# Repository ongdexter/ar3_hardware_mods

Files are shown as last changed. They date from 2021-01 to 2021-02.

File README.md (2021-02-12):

# AR3 Hardware Mods
Some modifications that I've made to the AR3 hardware. They are designed to be added on with minimal disassembly.

## Inductive Limit Switches
I repositioned the J5 limit switch to calibrate directly against the J6 bearing cap, which should be more accurate than using the belt carrier. I also took the opportunity to try out an inductive sensor, which I thought would be easier to position for the calibration angle than the mechanical switches. Having inductive limit switches will also help avoid cases of damaged or bent limit switches. It seems to have worked well so I'll eventually redesign and replace the other limit switches as well.

(https://www.youtube.com/watch?v=8Dm-i5OytqE "J5 Inductive Limit Switch")

-----

### J5 Limit Switch
* I use an **NJK-5002C** sensor along with the provided 10x2mm magnet though any other of similar dimensions that runs on 5V should work fine as a drop-in replacement, take note if you're getting an NO or NC one, you will have to make changes in the firmware accordingly
* Magnet mount will be secured to the J6 bearing cap with two M4x10 flathead screw, replacing the existing set screws
* Magnet can be press fit into the magnet mount  
  **NOTE**: be sure to mount it in the orientation with the correct polarity, test with the sensor first
* Sensor mount can be secured to the J6 main bearing arm with two M4x20 flathead screws, replacing the existing ones
* The sensor mount is designed to have just enough tolerance for the sensor to slide up and down with some force applied, this is to allow you to adjust the distance of the sensor from the magnet to calibrate the sensitivity. You'll want to adjust it such that the sensor is triggered only when the magnet is directly above
* The bearing cap is not fixed directly to the J6 housing so you'll have to manually rotate it so that the top and bottom screws are vertically aligned (see the first image below). This may require some trial-and-error - a good way I've found is to calibrate against the limit switch, send J5 to the 0-degree position through software, and then check if the J6 housing is aligned against the J5 cover spacer. After a good alignment is achieved, however, the bearing cap rotates with the J6 housing and can provide an accurate measurement of the rotation

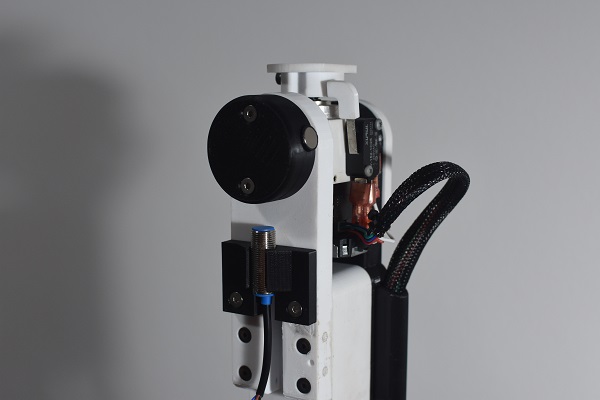
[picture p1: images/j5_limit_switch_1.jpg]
  
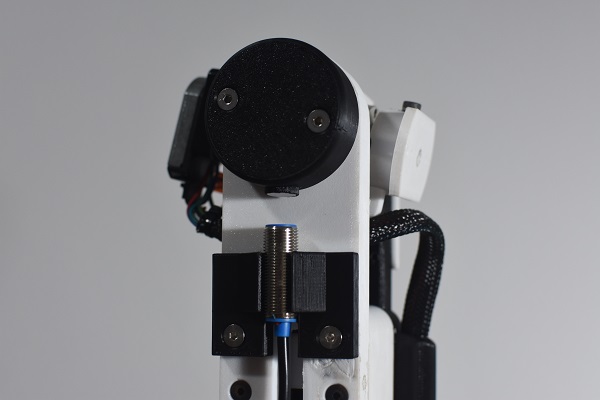
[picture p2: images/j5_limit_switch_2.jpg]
  

-----

## Joint Position Encoders
The original rotor encoder design provides good resolution and, despite backlash and other sources of inaccuracy, works well for applications that only require repeatability. Task positions can be taught and the actual joint positions do not matter too much. However, goals produced by motion planning require accurate correspondence between the actual and intended positions of the arm. At the cost of some resolution, we can achieve much more accurate control of the arm with joint position encoders. With the AMT-102V encoders at the maximum 2048 pulses per revolution, we can get 8192 counts with quadrature decoding, giving us a respectable resolution of 0.05 degrees per encoder count which is acceptable given that there are probably other more significant sources of error.

-----

### J2 Joint Encoder
* The spindle adapter can be screwed over the existing J2 drive spindle, replacing every other screw. You'll need longer M3 flathead screws
* Glue the two parts of the assembly together
* The entire piece will snap on the the J2 turret housing

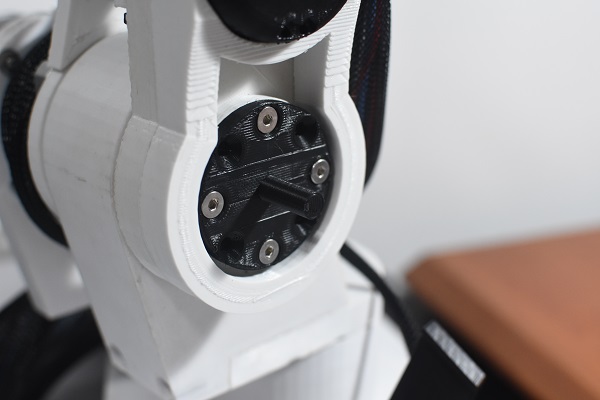
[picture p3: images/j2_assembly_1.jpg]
  
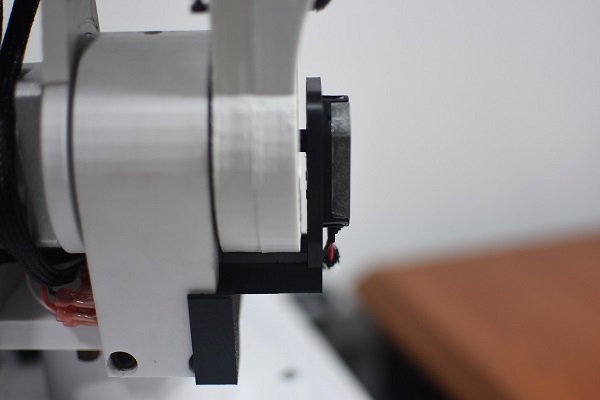
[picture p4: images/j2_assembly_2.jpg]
  
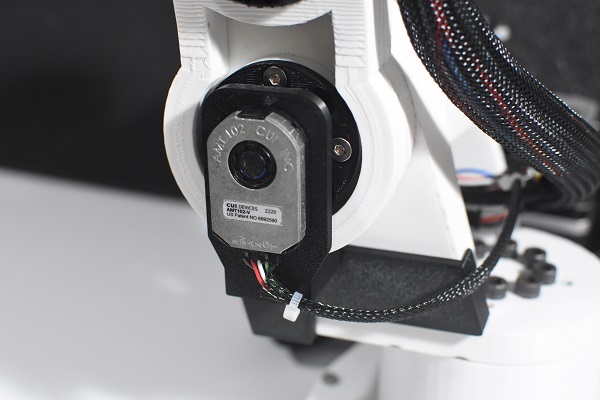
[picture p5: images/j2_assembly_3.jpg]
  

-----

### J5 Joint Encoder
* You can just glue the extension on to the J6 housing
* You'll want to use the longer M3 screws for the covers to secure the adapter
* I chose to leave the wires outside but with a little more effort you could squeeze them into the cover spacer and make everything a little neater

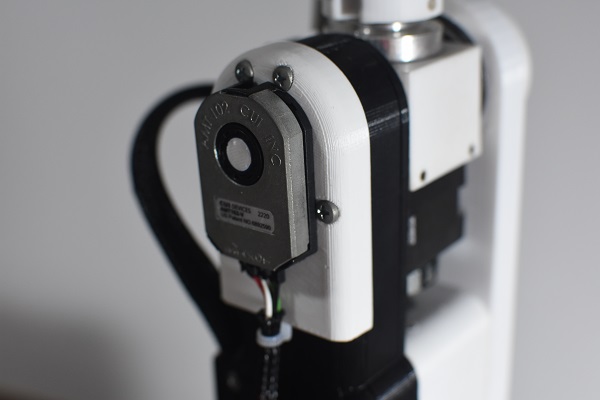
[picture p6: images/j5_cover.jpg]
  

-----

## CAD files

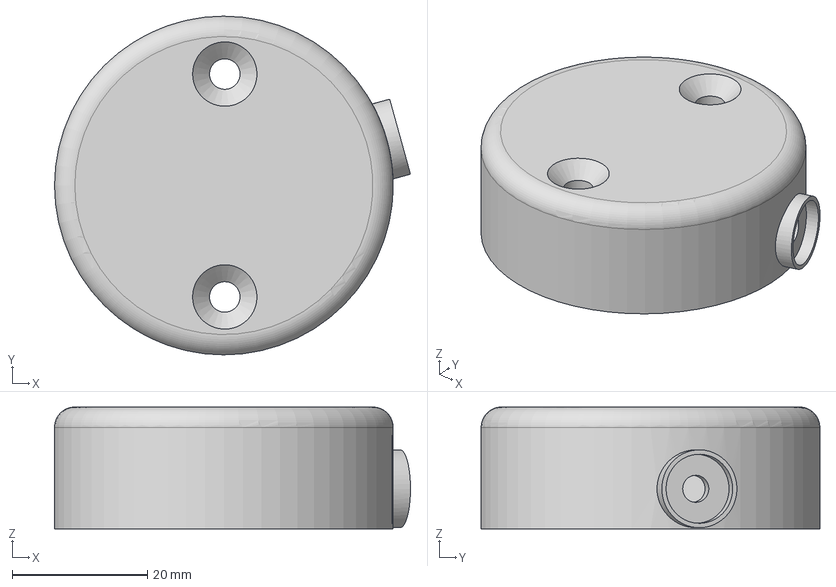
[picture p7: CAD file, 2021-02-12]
joint_limit_switches/J5/J5 limit switch magnet mount.step
52.6 x 50.0 x 18.0 mm

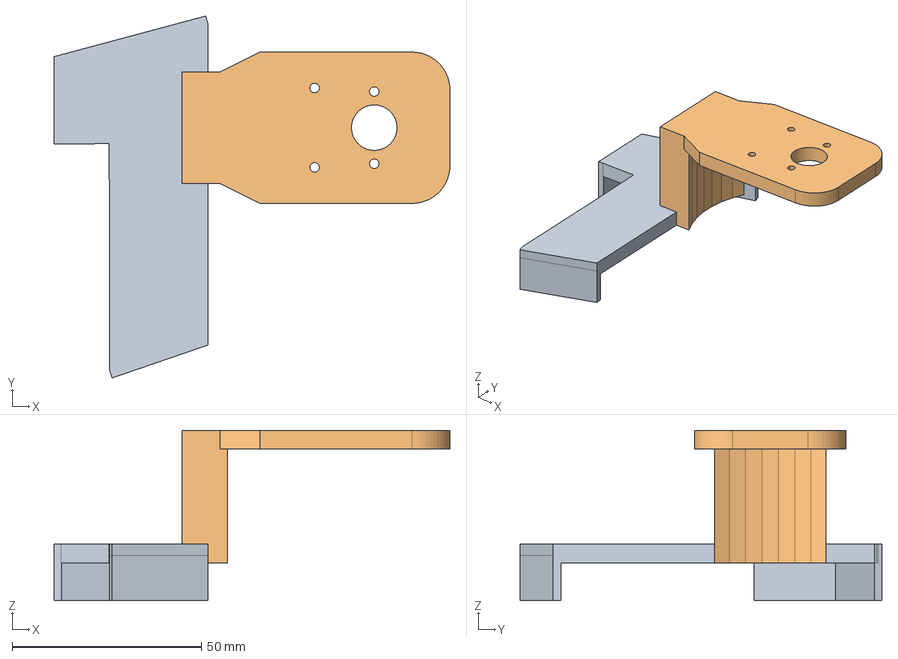
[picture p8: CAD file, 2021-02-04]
joint_position_encoders/J2/J2 joint encoder adapter mount.step
104.6 x 95.6 x 45.0 mm

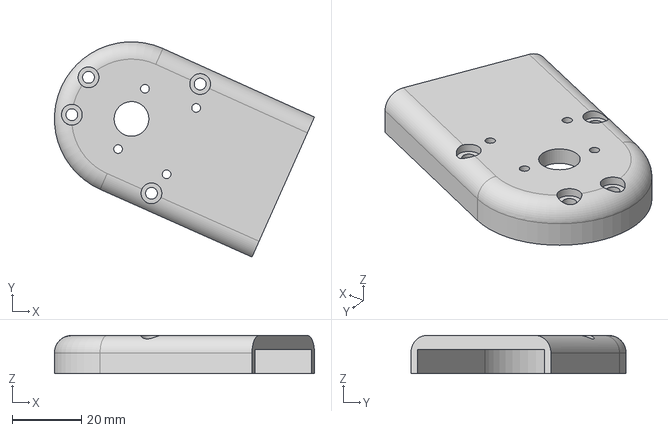
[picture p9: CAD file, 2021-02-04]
joint_position_encoders/J5/J5 joint encoder adapter mount.step
75.0 x 62.1 x 11.0 mm

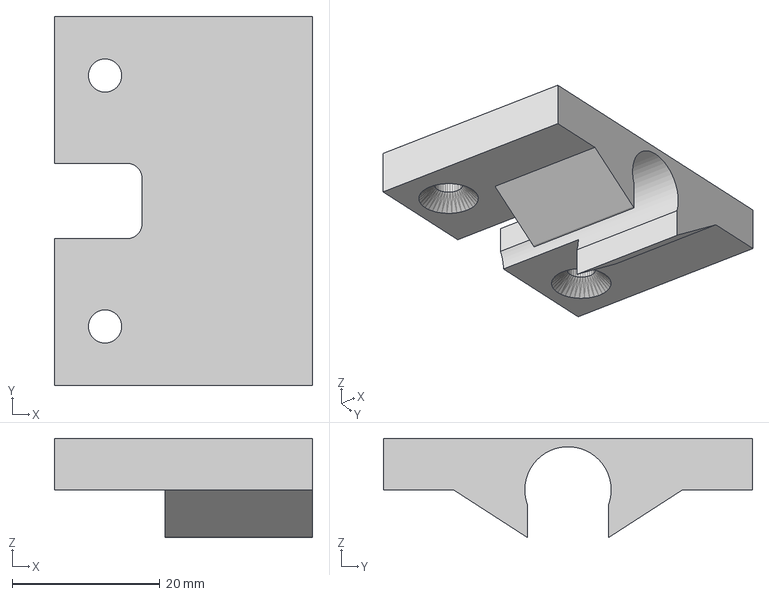
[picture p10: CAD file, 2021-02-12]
joint_limit_switches/J5/J5 limit switch sensor mount.step
35.0 x 50.0 x 13.5 mm

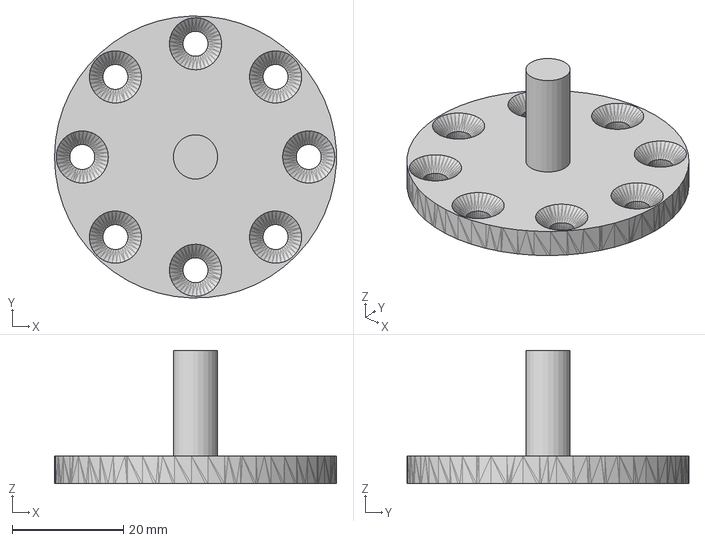
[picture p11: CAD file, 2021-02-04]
joint_position_encoders/J2/J2 joint encoder spindle adapter.step
50.8 x 50.8 x 24.0 mm

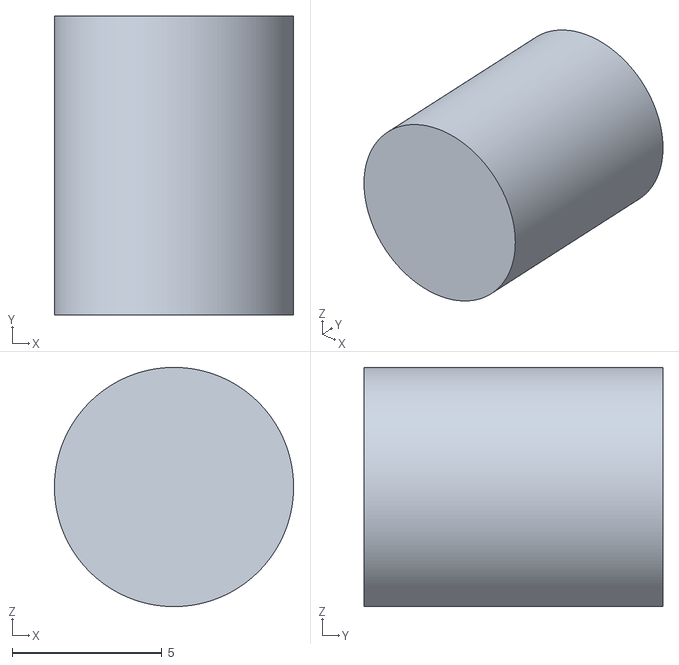
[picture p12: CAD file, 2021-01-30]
joint_position_encoders/J5/J5 joint encoder extension.stl
8.00 x 10.0 x 8.00

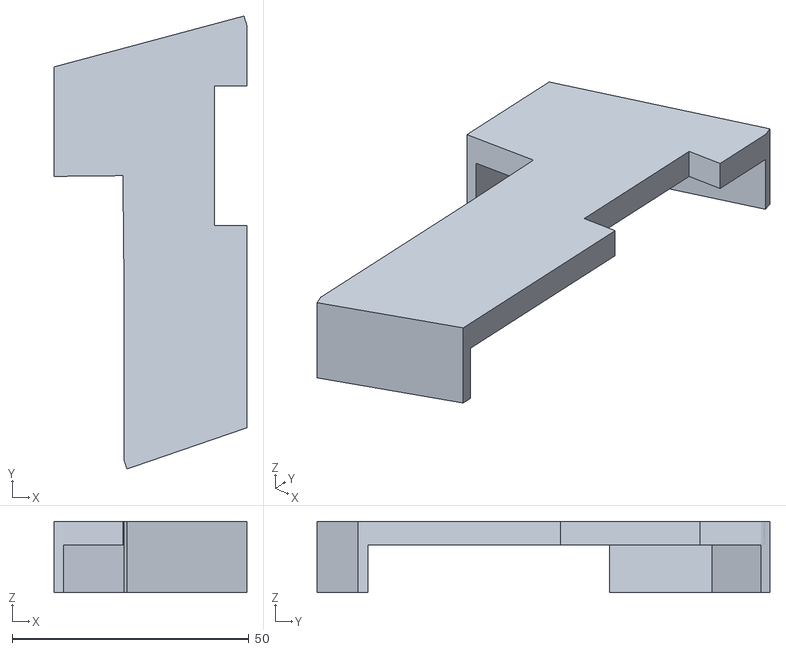
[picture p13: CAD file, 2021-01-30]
joint_position_encoders/J2/J2 joint encoder adapter mount part 1.stl
40.6 x 95.6 x 15.0

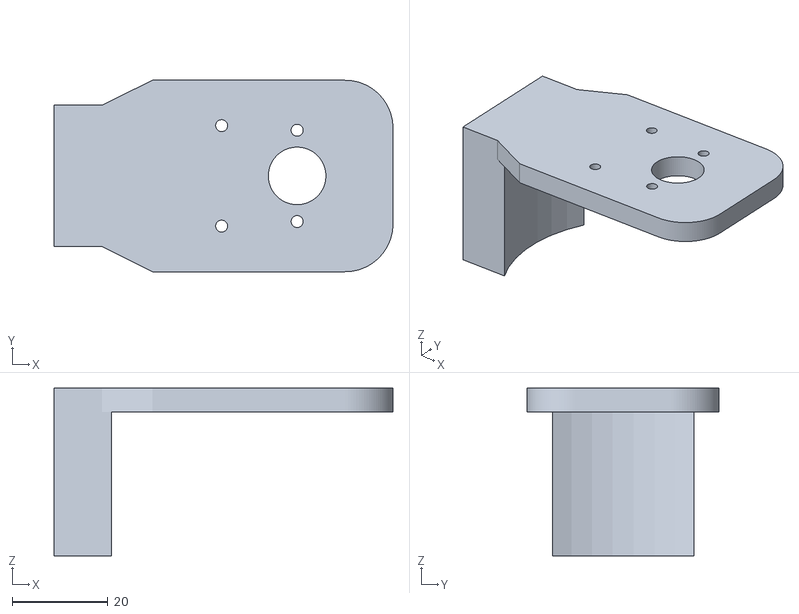
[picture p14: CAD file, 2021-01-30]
joint_position_encoders/J2/J2 joint encoder adapter mount part 2.stl
70.7 x 40.0 x 35.0

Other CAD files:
joint_limit_switches/J5/J5 limit switch magnet mount.f3d
joint_limit_switches/J5/J5 limit switch magnet mount.stl
joint_limit_switches/J5/J5 limit switch sensor mount.f3d
joint_limit_switches/J5/J5 limit switch sensor mount.stl
joint_position_encoders/J2/J2 joint encoder adapter mount.f3d
joint_position_encoders/J2/J2 joint encoder spindle adapter.f3d
joint_position_encoders/J2/J2 joint encoder spindle adapter.stl
joint_position_encoders/J5/J5 joint encoder adapter mount.f3d
joint_position_encoders/J5/J5 joint encoder adapter mount.stl

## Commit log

2021-01-30 J2 and J5 joint encoders
    [J2 joint encoder adapter part 1.stl, J2 joint encoder adapter part 2.stl, J2 joint encoder spindle adapter.stl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]
2021-01-30 Updated joint encoder descriptions
2021-02-04 Added step and f3d files
    [J2 joint encoder adapter mount part 1.stl, J2 joint encoder adapter mount part 2.stl, J2 joint encoder adapter mount.f3d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]
2021-02-12 Added J5 inductive limit switch
    [J5 limit switch magnet mount.f3d, J5 limit switch magnet mount.step, J5 limit switch magnet mount.stl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]
2021-02-12 Added point on bearing cap positioning for J5 limit switch
2021-02-12 Inductive limit switches
2021-02-12 Added video of J5 switch
